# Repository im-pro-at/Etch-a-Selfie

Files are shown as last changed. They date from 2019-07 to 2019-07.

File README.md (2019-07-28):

# Etch-a-Selfie
ESP32_CAM meets Etch-A-Sketch => Etch-a-Selfie

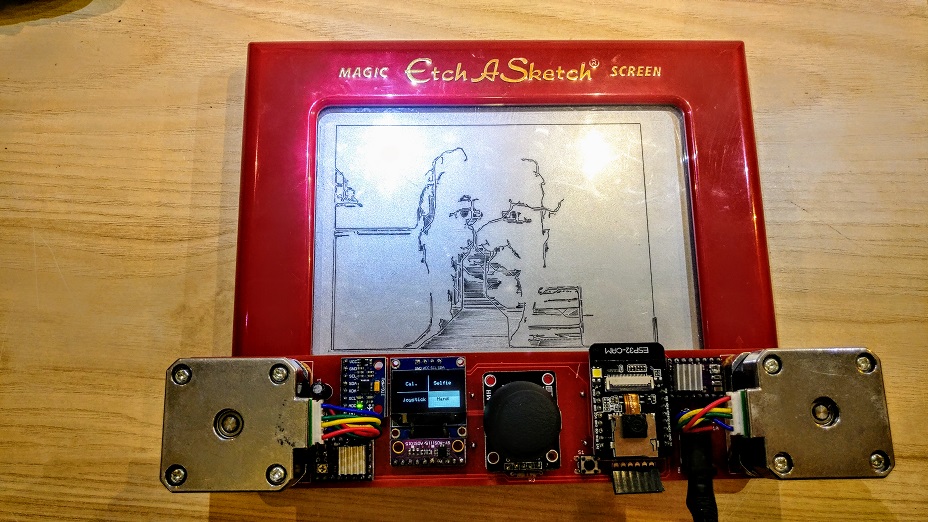
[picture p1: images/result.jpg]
result


## System Overview

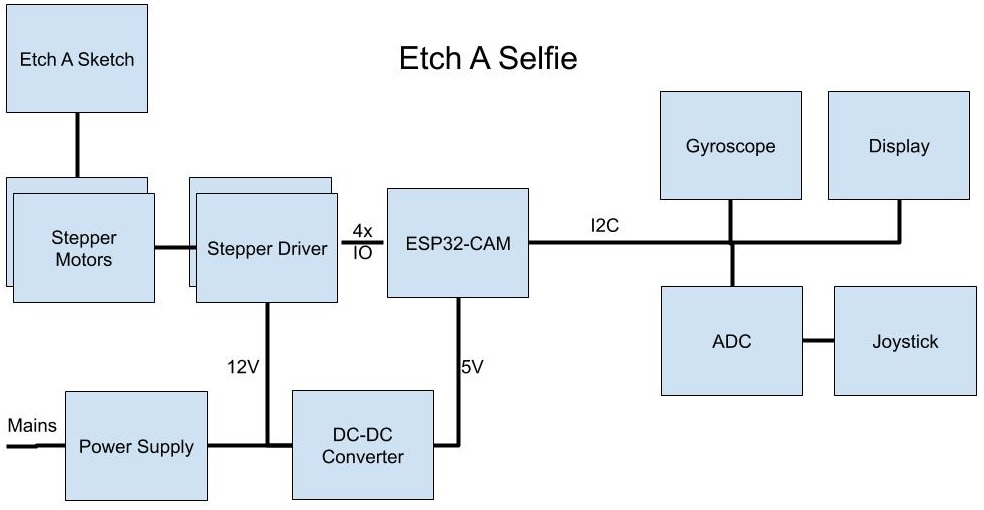
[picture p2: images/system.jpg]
system


## Software

The Software uses [GRBL](https://github.com/bdring/Grbl_Esp32) to controll the stepper motors.

A test implementation in JavaScript of the algorithms used is available [here](https://etch-a-selfie.im-pro.at/).

[Used Libraries](Sketch/ReadMe.md)

## BOM

[here](PCB/BOM.md)

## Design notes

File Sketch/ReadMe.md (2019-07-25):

# Versions 

| Name | Version |
| --- | --- |
| Arduino IDE | 1.8.9 |
| ESP32 core | 1.0.2 |
| adafruit/Adafruit-GFX-Library | 1.5.6 |
| adafruit/Adafruit_SSD1306 | 1.3.0 |
| tockn/MPU6050_tockn | 1.5.2 |
| adafruit/Adafruit_ADS1X15 | 1.0.1 |

Later Version may work but are not tested ...

# Settings

| Name | Setting |
| --- | --- |
| Board | ESP32 Wrover Module |
| Upload Speed | 921600 |
| Flash Frequency | 80MHz |
| Flash Mode | QIO |
| Partion Scheme | Huge APP (3Mb No OTA) |
| Core Debug Level | None |

# Flashing

Look [here](https://github.com/raphaelbs/esp32-cam-ai-thinker#flashing)

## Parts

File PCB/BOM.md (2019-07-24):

# Bill of materials

| # |  Price | Description |
| ---- | -----: | --- |
| 1 | 36,99€ | [Etch-A-Sketch Classic](https://www.amazon.de/Spin-Master-20083952-Etch-A-Sketch-Classic/dp/B01N1ZVYDM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) |
| 1 |  6.76€ | [PCB form JLCPCB](https://jlcpcb.com) |
| 1 |  6,21€ | [Geekcreit® ESP32-CAM WiFi + bluetooth Camera Module](https://www.banggood.com/Geekcreit-ESP32-CAM-WiFi-bluetooth-Camera-Module-Development-Board-ESP32-With-Camera-Module-OV2640-p-1394679.html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) |
| 1 |  1,40€ | [2596S LM2596S 3A Adjustable Step-down DC-DC Power Supply Module](https://www.banggood.com/1pcs-2596S-LM2596S-3A-Adjustable-Step-down-DC-DC-Power-Supply-Module-p-1213135.html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) |
| 1 |  4,43€ | [Geekcreit® 1.3 Inch 4Pin White OLED LCD Display 12864 IIC](https://www.banggood.com/1_3-Inch-4Pin-White-OLED-LCD-Display-12864-IIC-I2C-Interface-Module-For-Arduino-p-1067874.html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) |
| 1 |  1,32€ | [6DOF MPU-6050 3 Axis Gyro With Accelerometer Sensor](https://www.banggood.com/6DOF-MPU-6050-3-Axis-Gyro-With-Accelerometer-Sensor-Module-For-Arduino-p-80862.html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) |
| 1 |  1,34€ | [PS2 Game Joystick Module For Arduino](https://www.banggood.com/PS2-Game-Joystick-Module-For-Arduino-p-76465.html?rmmds=search&cur_warehouse=CN) |
| 1 |  3,53€ | [I2C ADS1115 16 Bit ADC 4 Channel Module](https://www.banggood.com/I2C-ADS1115-16-Bit-ADC-4-Channel-Module-With-Programmable-Gain-Amplifier-For-Arduino-RPi-p-1110588.html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) |
| 1 |  1,50€ | [DC Jack 5.5x2.1mm](https://www.banggood.com/10pcs-5_5-x-2_1mm-DC-Power-Supply-Female-Jack-Socket-p-1062018.html?cur_warehouse=CN) |
| 2 |  1,66€ | [5mm x 6mm Aluminum Flexible Shaft Coupling OD19mm x L25mm](https://www.banggood.com/5mm-x-6mm-Aluminum-Flexible-Shaft-Coupling-OD19mm-x-L25mm-CNC-Stepper-Motor-Coupler-Connector-p-993559.html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) |
| 2 |  2,12€ | [Geekcreit® 3D Printer Stepstick DRV8825 Stepper Driver Reprap 4 Layer PCB](https://www.banggood.com/Geekcreit-3D-Printer-Stepstick-DRV8825-Stepper-Motor-Driver-Reprap-4-Layer-PCB-p-920162.html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) |
| 2 |  6,27€ | [HANPOSE 17HS2408 28mm Nema 17 Stepper Motor 42 Motor 42BYGH 0.6A 12N.cm](https://www.banggood.com/HANPOSE-28mm-Nema-17-Stepper-Motor-42-Motor-17HS2408-42BYGH-0_6A-12N_cm-4-lead-For-CNC-Laser-3D-Printer-Motor-p-1415423.html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) |
| 1 |  3,94€ | [AC 100-240V Converter Adapter 12V 2A 24W Power Supply](https://www.banggood.com/AC-100-240V-Converter-Adapter-12V-2A-24W-Power-Supply-For-LED-Strip-p-1006925.html?ID=43100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) |
| 1 |  1,28€ | [2.54mm Single Row Male Pin Header](https://www.banggood.com/10-Pcs-40-Pin-2_54mm-Single-Row-Male-Pin-Header-Strip-For-Arduino-p-918427.html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) |
| 3 | - | 4k7 Ohm Resistor 1/4W |
| 4 | - | M3 screw 8mm length |
| 2 |  1,60€ | [Cork Gasket (Optional)](https://www.banggood.com/5PCS-4242mm-Cork-Gasket-Nema-17-Stepper-Motor-Damper-For-42-Motor-Absorber-3D-Printer-Part-p-1446977.html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) |
| 2 | - | 100µF 35V Capacitor E2,5-6 (Optional) |
| | | |
| | ~89€ | TOTAL |

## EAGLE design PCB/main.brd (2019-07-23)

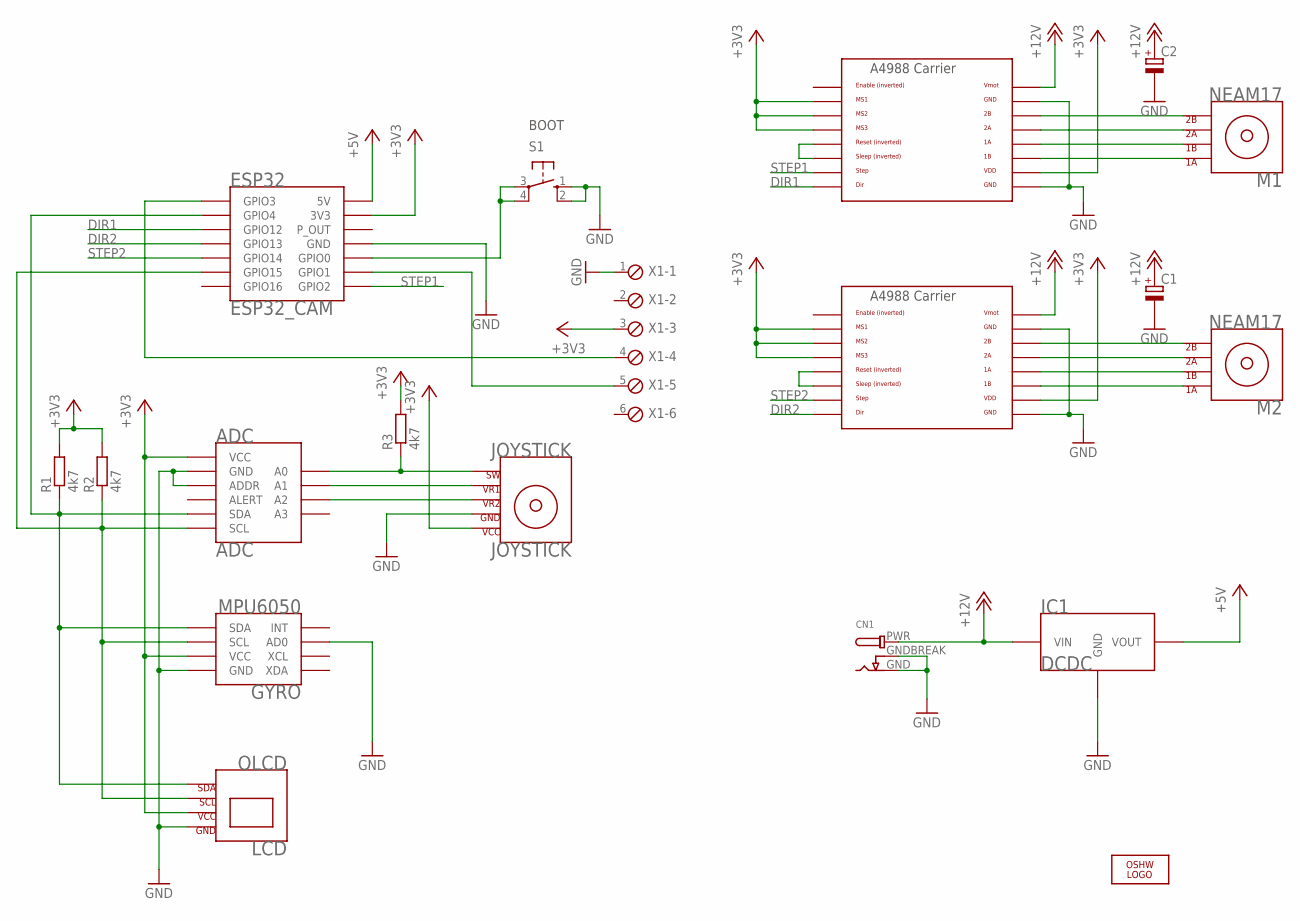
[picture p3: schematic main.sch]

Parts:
ADC: ADC
C1, C2: CPOL-EUE2.5-6; E2,5-6
CN1: DCBARRELPTH; DCJACK_2MM_PTH
ESP32: ESP32_CAM
GYRO: MPU6050
IC1: DCDC
IC2, IC3: A4988BREAKOUT
JOYSTICK: JOYSTICK
LCD: OLCD
LOGO1: OHW-LOGO_OSHW_LOGO_FILLX0350-NT; OHW-LOGO_OSHW_FILLX350_NOTEXT
M1, M2: NEAM17; NEMA17
R1, R2, R3: 4k7; 0207/10
S1: 10-XX; B3F-10XX
X1: MPT6; 6POL254

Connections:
+3V3: ADC.VCC, ESP32.3V3, GYRO.VCC, IC2.MS1, IC2.MS2, IC2.MS3, IC2.VDD, IC3.MS1, IC3.MS2, IC3.MS3, IC3.VDD, JOYSTICK.VCC, LCD.VCC, R1.2, R2.2, R3.2, X1.3
+5V: ESP32.5V, IC1.VOUT
+12V: C1.+, C2.+, CN1.PWR, IC1.VIN, IC2.VMOT, IC3.VMOT
DIR1: ESP32.GPIO12, IC2.DIR
DIR2: ESP32.GPIO13, IC3.DIR
GND: ADC.ADDR, ADC.GND, C1.-, C2.-, CN1.GND, CN1.GNDBREAK, ESP32.GND1 (GND), ESP32.GND2 (GND), ESP32.GND3 (GND), GYRO.AD0, GYRO.GND, IC1.GND1 (GND), IC1.GND2 (GND), IC2.GND, IC2.GND@0 (GND), IC3.GND, IC3.GND@0 (GND), JOYSTICK.GND, LCD.GND, S1.1 (S), S1.2 (S1), X1.1
unnamed: IC2.1B, M1.1A
unnamed: IC2.RST, IC2.SLP (SLEEP)
unnamed: IC2.2B, M1.2B
unnamed: IC2.2A, M1.2A
unnamed: IC2.1A, M1.1B
unnamed: IC3.RST, IC3.SLP (SLEEP)
unnamed: IC3.2B, M2.2B
unnamed: IC3.2A, M2.2A
unnamed: IC3.1A, M2.1B
unnamed: IC3.1B, M2.1A
unnamed: ESP32.GPIO1, X1.5
unnamed: ESP32.GPIO3, X1.4
unnamed: ESP32.GPIO0, S1.3, S1.4 (P1)
unnamed: ADC.A0, JOYSTICK.SW, R3.1
unnamed: ADC.A1, JOYSTICK.VR1
unnamed: ADC.A2, JOYSTICK.VR2
unnamed: ADC.SCL, ESP32.GPIO15, GYRO.SCL, LCD.SCL, R2.1
unnamed: ADC.SDA, ESP32.GPIO4, GYRO.SDA, LCD.SDA, R1.1
STEP1: ESP32.GPIO2, IC2.STEP
STEP2: ESP32.GPIO14, IC3.STEP

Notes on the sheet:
BOOT

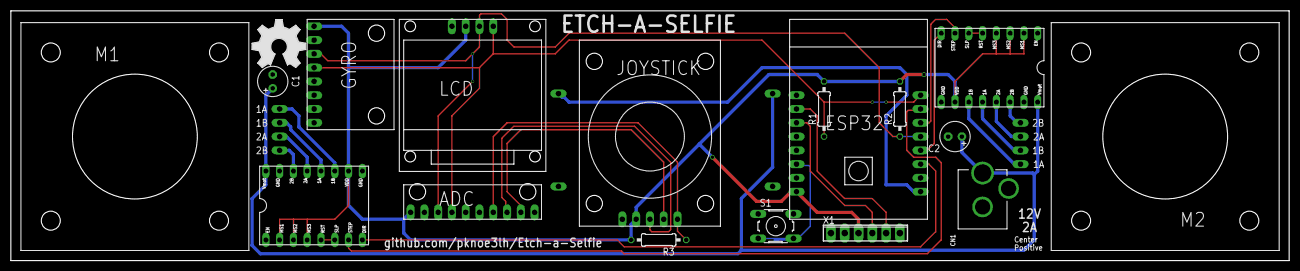
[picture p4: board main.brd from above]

Board: 2 copper layers, 235.6 x 46.0 mm, 19 parts (1 on the bottom side), 26 nets.

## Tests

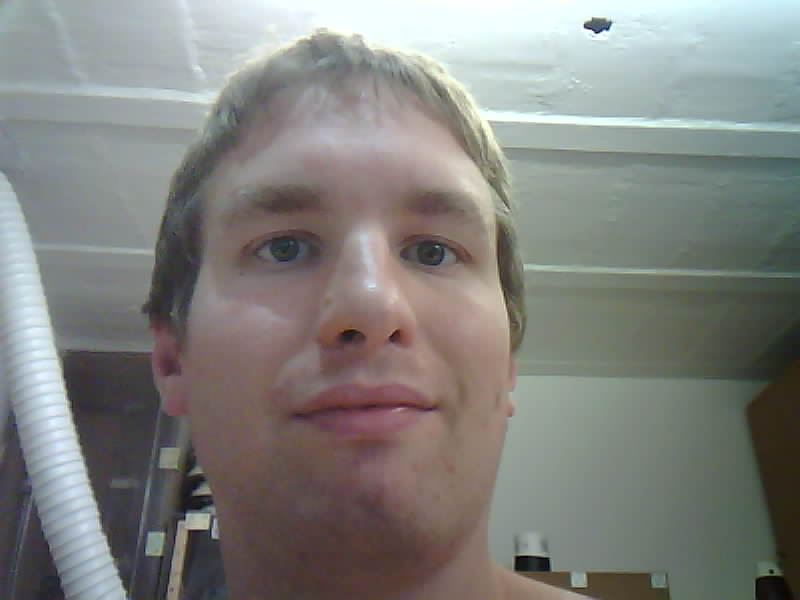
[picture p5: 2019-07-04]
AlgorithmTest/test.jpg

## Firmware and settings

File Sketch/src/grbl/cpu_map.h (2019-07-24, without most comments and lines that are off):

#ifdef CPU_MAP_ESP32
		#define CPU_MAP_NAME "CPU_MAP_ESP32"
		#define X_STEP_PIN      	GPIO_NUM_12
		#define X_DIRECTION_PIN  	GPIO_NUM_26
		#define X_RMT_CHANNEL		0
		#define Y_STEP_PIN      	GPIO_NUM_14
		#define Y_DIRECTION_PIN   	GPIO_NUM_25
		#define Y_RMT_CHANNEL		1
		#define Z_STEP_PIN      	GPIO_NUM_27
		#define Z_DIRECTION_PIN   	GPIO_NUM_33
		#define Z_RMT_CHANNEL		2
		#define STEPPERS_DISABLE_PIN GPIO_NUM_13
		#define COOLANT_FLOOD_PIN 	GPIO_NUM_16
		#define SPINDLE_PWM_PIN    GPIO_NUM_17
		#define SPINDLE_PWM_CHANNEL 0
		#define SPINDLE_PWM_BASE_FREQ 5000 // Hz
		#define SPINDLE_PWM_BIT_PRECISION 8   // be sure to match this with SPINDLE_PWM_MAX_VALUE
		#define SPINDLE_PWM_OFF_VALUE     0
		#define SPINDLE_PWM_MAX_VALUE     255 // (2^SPINDLE_PWM_BIT_PRECISION)
				#define SPINDLE_PWM_MIN_VALUE   1   // Must be greater than zero.
		#define SPINDLE_ENABLE_PIN	GPIO_NUM_22
		#define SPINDLE_PWM_RANGE         (SPINDLE_PWM_MAX_VALUE-SPINDLE_PWM_MIN_VALUE)
		#define X_LIMIT_PIN      	GPIO_NUM_2
		#define Y_LIMIT_PIN      	GPIO_NUM_4
		#define Z_LIMIT_PIN     	GPIO_NUM_15
		#define LIMIT_MASK      	B111
		#define PROBE_PIN       	GPIO_NUM_32
		#define CONTROL_SAFETY_DOOR_PIN   GPIO_NUM_35  // needs external pullup
		#define CONTROL_RESET_PIN         GPIO_NUM_34  // needs external pullup
		#define CONTROL_FEED_HOLD_PIN     GPIO_NUM_36  // needs external pullup
		#define CONTROL_CYCLE_START_PIN   GPIO_NUM_39  // needs external pullup
#endif
#ifdef CPU_MAP_ESP32_ETCH_A_SELFIE
		#define CPU_MAP_NAME "CPU_MAP_ESP32_ETCH_A_SELFIE"
		#define X_STEP_PIN      	GPIO_NUM_2
		#define X_DIRECTION_PIN  	GPIO_NUM_12
		#define Y_STEP_PIN      	GPIO_NUM_14
		#define Y_DIRECTION_PIN   GPIO_NUM_13
		#define SPINDLE_PWM_CHANNEL 0
		#define SPINDLE_PWM_BASE_FREQ 5000 // Hz
		#define SPINDLE_PWM_BIT_PRECISION 8   // be sure to match this with SPINDLE_PWM_MAX_VALUE
		#define SPINDLE_PWM_OFF_VALUE     0
		#define SPINDLE_PWM_MAX_VALUE     255 // (2^SPINDLE_PWM_BIT_PRECISION)
		#ifndef SPINDLE_PWM_MIN_VALUE
				#define SPINDLE_PWM_MIN_VALUE   1   // Must be greater than zero.
		#endif
		#define SPINDLE_PWM_RANGE         (SPINDLE_PWM_MAX_VALUE-SPINDLE_PWM_MIN_VALUE)
		#define LIMIT_MASK      	B111
		#define PROBE_PIN       	GPIO_NUM_32
		#ifdef DEFAULTS_GENERIC
			#undef DEFAULTS_GENERIC  // undefine generic then define each default below
		#endif
		#define DEFAULT_STEP_PULSE_MICROSECONDS 3
		#define DEFAULT_STEPPER_IDLE_LOCK_TIME 250 // stay on
		#define DEFAULT_STEPPING_INVERT_MASK 0 // uint8_t
		#define DEFAULT_DIRECTION_INVERT_MASK 1 // Invert x
		#define DEFAULT_INVERT_ST_ENABLE 0 // boolean
		#define DEFAULT_INVERT_LIMIT_PINS 1 // boolean
		#define DEFAULT_INVERT_PROBE_PIN 0 // boolean
		#define DEFAULT_STATUS_REPORT_MASK 1
		#define DEFAULT_JUNCTION_DEVIATION 0.01 // mm
		#define DEFAULT_ARC_TOLERANCE 0.002 // mm
		#define DEFAULT_REPORT_INCHES 0 // false
		#define DEFAULT_SOFT_LIMIT_ENABLE 0 // false
		#define DEFAULT_HARD_LIMIT_ENABLE 0  // false
		#define DEFAULT_HOMING_ENABLE 0
		#define DEFAULT_HOMING_DIR_MASK 0 // move positive dir Z, negative X,Y
		#define DEFAULT_HOMING_FEED_RATE 200.0 // mm/min
		#define DEFAULT_HOMING_SEEK_RATE 1000.0 // mm/min
		#define DEFAULT_HOMING_DEBOUNCE_DELAY 250 // msec (0-65k)
		#define DEFAULT_HOMING_PULLOFF 3.0 // mm
		#define DEFAULT_SPINDLE_RPM_MAX 1000.0 // rpm
		#define DEFAULT_SPINDLE_RPM_MIN 0.0 // rpm
		#define DEFAULT_LASER_MODE 0 // false
		#define DEFAULT_X_STEPS_PER_MM 44.44
		#define DEFAULT_Y_STEPS_PER_MM 44.44
		#define DEFAULT_Z_STEPS_PER_MM 100.0
		#define DEFAULT_X_MAX_RATE 30000.0 // mm/min
		#define DEFAULT_Y_MAX_RATE 30000.0 // mm/min
		#define DEFAULT_Z_MAX_RATE 5000.0 // mm/min
		#define DEFAULT_X_ACCELERATION (5000.0*60*60)
		#define DEFAULT_Y_ACCELERATION (5000.0*60*60)
		#define DEFAULT_Z_ACCELERATION (50.0*60*60)
		#define DEFAULT_X_MAX_TRAVEL 300.0 // mm NOTE: Must be a positive value.
		#define DEFAULT_Y_MAX_TRAVEL 300.0 // mm NOTE: Must be a positive value.
		#define DEFAULT_Z_MAX_TRAVEL 100.0 // This is percent in servo mode...used for calibration
#endif
#ifdef CPU_MAP_ESP32_ESC_SPINDLE
		#define CPU_MAP_NAME "CPU_MAP_ESP32_ESC_SPINDLE"
		#define X_STEP_PIN      	GPIO_NUM_12
		#define X_DIRECTION_PIN  	GPIO_NUM_26
		#define X_RMT_CHANNEL		0
		#define Y_STEP_PIN      	GPIO_NUM_14
		#define Y_DIRECTION_PIN   	GPIO_NUM_25
		#define Y_RMT_CHANNEL		1
		#define Z_STEP_PIN      	GPIO_NUM_27
		#define Z_DIRECTION_PIN   	GPIO_NUM_33
		#define Z_RMT_CHANNEL		2
		#define STEPPERS_DISABLE_PIN GPIO_NUM_13
		#define COOLANT_FLOOD_PIN 	GPIO_NUM_16
		#define SPINDLE_PWM_PIN    GPIO_NUM_17
		#define SPINDLE_PWM_CHANNEL 0
		#define SPINDLE_PWM_BASE_FREQ 50 // Hz for ESC
		#define SPINDLE_PWM_BIT_PRECISION 16   // 16 bit required for ESC
		#define SPINDLE_PULSE_RES_COUNT 65535
		#define ESC_MIN_PULSE_SEC 0.001 // min pulse in seconds (OK to tune this one)
		#define ESC_MAX_PULSE_SEC 0.002 // max pulse in seconds (OK to tune this one)
		#define ESC_TIME_PER_BIT  ((1.0 / (float)SPINDLE_PWM_BASE_FREQ) / ((float)SPINDLE_PULSE_RES_COUNT) ) // seconds
		#define SPINDLE_PWM_OFF_VALUE    (uint16_t)(ESC_MIN_PULSE_SEC / ESC_TIME_PER_BIT) // in timer counts
		#define SPINDLE_PWM_MAX_VALUE    (uint16_t)(ESC_MAX_PULSE_SEC / ESC_TIME_PER_BIT) // in timer counts
		#ifndef SPINDLE_PWM_MIN_VALUE
				#define SPINDLE_PWM_MIN_VALUE   SPINDLE_PWM_OFF_VALUE   // Must be greater than zero.
		#endif
		#define SPINDLE_PWM_RANGE         (SPINDLE_PWM_MAX_VALUE-SPINDLE_PWM_MIN_VALUE)
		#define SPINDLE_ENABLE_PIN	GPIO_NUM_22
		#define X_LIMIT_PIN      	GPIO_NUM_2
		#define Y_LIMIT_PIN      	GPIO_NUM_4
		#define Z_LIMIT_PIN     	GPIO_NUM_15
		#define LIMIT_MASK      	B111
		#define PROBE_PIN       	GPIO_NUM_32
		#define CONTROL_SAFETY_DOOR_PIN   GPIO_NUM_35  // needs external pullup
		#define CONTROL_RESET_PIN         GPIO_NUM_34  // needs external pullup
		#define CONTROL_FEED_HOLD_PIN     GPIO_NUM_36  // needs external pullup
		#define CONTROL_CYCLE_START_PIN   GPIO_NUM_39  // needs external pullup
#endif
#ifdef CPU_MAP_PEN_LASER  // The Buildlog.net pen laser controller V1
		#define CPU_MAP_NAME "CPU_MAP_PEN_LASER"
		#define PEN_LASER_V2
		#define X_STEP_PIN      GPIO_NUM_12
		#define Y_STEP_PIN      GPIO_NUM_14
		#define X_DIRECTION_PIN   GPIO_NUM_26
		#define Y_DIRECTION_PIN   GPIO_NUM_25
		#define STEPPERS_DISABLE_PIN GPIO_NUM_13
		#ifdef PEN_LASER_V2
			#define X_LIMIT_PIN      	GPIO_NUM_15
		#endif
		#define Y_LIMIT_PIN      	GPIO_NUM_4
		#define LIMIT_MASK      	B11
		#define SPINDLE_PWM_PIN    GPIO_NUM_17 // Laser PWM
		#define SPINDLE_PWM_CHANNEL 0
		#define SPINDLE_PWM_BASE_FREQ 5000 // Hz
		#define SPINDLE_PWM_BIT_PRECISION 8   // be sure to match this with SPINDLE_PWM_MAX_VALUE
		#define SPINDLE_PWM_OFF_VALUE     0
		#define SPINDLE_PWM_MAX_VALUE     255 // (2^SPINDLE_PWM_BIT_PRECISION)
		#ifndef SPINDLE_PWM_MIN_VALUE
				#define SPINDLE_PWM_MIN_VALUE   1   // Must be greater than zero.
		#endif
		#define SPINDLE_PWM_RANGE         (SPINDLE_PWM_MAX_VALUE-SPINDLE_PWM_MIN_VALUE)
		#define SERVO_PEN_PIN 					GPIO_NUM_27
		#ifdef DEFAULTS_GENERIC
			#undef DEFAULTS_GENERIC  // undefine generic then define each default below
		#endif
		#define DEFAULT_STEP_PULSE_MICROSECONDS 3
		#define DEFAULT_STEPPER_IDLE_LOCK_TIME 250 // stay on
		#define DEFAULT_STEPPING_INVERT_MASK 0 // uint8_t
		#define DEFAULT_DIRECTION_INVERT_MASK 0 // uint8_t
		#define DEFAULT_INVERT_ST_ENABLE 0 // boolean
		#define DEFAULT_INVERT_LIMIT_PINS 1 // boolean
		#define DEFAULT_INVERT_PROBE_PIN 0 // boolean
		#define DEFAULT_STATUS_REPORT_MASK 1
		#define DEFAULT_JUNCTION_DEVIATION 0.01 // mm
		#define DEFAULT_ARC_TOLERANCE 0.002 // mm
		#define DEFAULT_REPORT_INCHES 0 // false
		#define DEFAULT_SOFT_LIMIT_ENABLE 0 // false
		#define DEFAULT_HARD_LIMIT_ENABLE 0  // false
		#define DEFAULT_HOMING_ENABLE 0
		#define DEFAULT_HOMING_DIR_MASK 0 // move positive dir Z, negative X,Y
		#define DEFAULT_HOMING_FEED_RATE 200.0 // mm/min
		#define DEFAULT_HOMING_SEEK_RATE 1000.0 // mm/min
		#define DEFAULT_HOMING_DEBOUNCE_DELAY 250 // msec (0-65k)
		#define DEFAULT_HOMING_PULLOFF 3.0 // mm
		#define DEFAULT_SPINDLE_RPM_MAX 1000.0 // rpm
		#define DEFAULT_SPINDLE_RPM_MIN 0.0 // rpm
		#define DEFAULT_LASER_MODE 0 // false
		#define DEFAULT_X_STEPS_PER_MM 80
		#define DEFAULT_Y_STEPS_PER_MM 80
		#define DEFAULT_Z_STEPS_PER_MM 100.0 // This is percent in servo mode...used for calibration
		#define DEFAULT_X_MAX_RATE 5000.0 // mm/min
		#define DEFAULT_Y_MAX_RATE 5000.0 // mm/min
		#define DEFAULT_Z_MAX_RATE 5000.0 // mm/min
		#define DEFAULT_X_ACCELERATION (50.0*60*60) // 10*60*60 mm/min^2 = 10 mm/sec^2
		#define DEFAULT_Y_ACCELERATION (50.0*60*60) // 10*60*60 mm/min^2 = 10 mm/sec^2
		#define DEFAULT_Z_ACCELERATION (50.0*60*60)
		#define DEFAULT_X_MAX_TRAVEL 300.0 // mm NOTE: Must be a positive value.
		#define DEFAULT_Y_MAX_TRAVEL 300.0 // mm NOTE: Must be a positive value.
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

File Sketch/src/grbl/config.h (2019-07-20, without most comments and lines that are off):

#define config_h
#include "grbl.h" // For Arduino IDE compatibility.
#define ESP_DEBUG
#define DEFAULTS_GENERIC
#define CPU_MAP_ESP32_ETCH_A_SELFIE // these are defined in cpu_map.h
#define VERBOSE_HELP // adds addition help info, but could confuse some senders
#define BAUD_RATE 115200
#define NAMESPACE "GRBL"
#define ESP_RADIO_MODE "RADIO_MODE"
#define ESP_RADIO_OFF 0
#define ESP_WIFI_STA 1
#define ESP_WIFI_AP  2
#define ESP_BT       3
    #undef ENABLE_NOTIFICATIONS
    #define DEFAULT_RADIO_MODE ESP_RADIO_OFF
#define CMD_RESET 0x18 // ctrl-x.
#define CMD_STATUS_REPORT '?'
#define CMD_CYCLE_START '~'
#define CMD_FEED_HOLD '!'
#define CMD_SAFETY_DOOR 0x84
#define CMD_JOG_CANCEL  0x85
#define CMD_DEBUG_REPORT 0x86 // Only when DEBUG enabled, sends debug report in '{}' braces.
#define CMD_FEED_OVR_RESET 0x90         // Restores feed override value to 100%.
#define CMD_FEED_OVR_COARSE_PLUS 0x91
#define CMD_FEED_OVR_COARSE_MINUS 0x92
#define CMD_FEED_OVR_FINE_PLUS  0x93
#define CMD_FEED_OVR_FINE_MINUS  0x94
#define CMD_RAPID_OVR_RESET 0x95        // Restores rapid override value to 100%.
#define CMD_RAPID_OVR_MEDIUM 0x96
#define CMD_RAPID_OVR_LOW 0x97
#define CMD_SPINDLE_OVR_RESET 0x99      // Restores spindle override value to 100%.
#define CMD_SPINDLE_OVR_COARSE_PLUS 0x9A
#define CMD_SPINDLE_OVR_COARSE_MINUS 0x9B
#define CMD_SPINDLE_OVR_FINE_PLUS 0x9C
#define CMD_SPINDLE_OVR_FINE_MINUS 0x9D
#define CMD_SPINDLE_OVR_STOP 0x9E
#define CMD_COOLANT_FLOOD_OVR_TOGGLE 0xA0
#define CMD_COOLANT_MIST_OVR_TOGGLE 0xA1
#define HOMING_INIT_LOCK // Comment to disable
#define HOMING_CYCLE_0 (1<<Z_AXIS)                // REQUIRED: First move Z to clear workspace.
#define HOMING_CYCLE_1 (1<<X_AXIS)
#define HOMING_CYCLE_2 (1<<Y_AXIS)
#define N_HOMING_LOCATE_CYCLE 1 // Integer (1-128)
#define HOMING_SINGLE_AXIS_COMMANDS // Default disabled. Uncomment to enable.
#define N_STARTUP_LINE 2 // Integer (1-2)
#define N_DECIMAL_COORDVALUE_INCH 4 // Coordinate or position value in inches
#define N_DECIMAL_COORDVALUE_MM   3 // Coordinate or position value in mm
#define N_DECIMAL_RATEVALUE_INCH  1 // Rate or velocity value in in/min
#define N_DECIMAL_RATEVALUE_MM    0 // Rate or velocity value in mm/min
#define N_DECIMAL_SETTINGVALUE    3 // Decimals for floating point setting values
#define N_DECIMAL_RPMVALUE        0 // RPM value in rotations per min.
#define ENABLE_SAFETY_DOOR_INPUT_PIN // ESP32 Leave this enabled for now .. code for undefined not ready
#define SAFETY_DOOR_SPINDLE_DELAY 4.0 // Float (seconds)
#define SAFETY_DOOR_COOLANT_DELAY 1.0 // Float (seconds)
#define INVERT_CONTROL_PIN_MASK   B1111
#define IGNORE_CONTROL_PINS
#define CHECK_LIMITS_AT_INIT
#define DEFAULT_FEED_OVERRIDE           100 // 100%. Don't change this value.
#define MAX_FEED_RATE_OVERRIDE          200 // Percent of programmed feed rate (100-255). Usually 120% or 200%
#define MIN_FEED_RATE_OVERRIDE           10 // Percent of programmed feed rate (1-100). Usually 50% or 1%
#define FEED_OVERRIDE_COARSE_INCREMENT   10 // (1-99). Usually 10%.
#define FEED_OVERRIDE_FINE_INCREMENT      1 // (1-99). Usually 1%.
#define DEFAULT_RAPID_OVERRIDE  100 // 100%. Don't change this value.
#define RAPID_OVERRIDE_MEDIUM    50 // Percent of rapid (1-99). Usually 50%.
#define RAPID_OVERRIDE_LOW       25 // Percent of rapid (1-99). Usually 25%.
#define DEFAULT_SPINDLE_SPEED_OVERRIDE    100 // 100%. Don't change this value.
#define MAX_SPINDLE_SPEED_OVERRIDE        200 // Percent of programmed spindle speed (100-255). Usually 200%.
#define MIN_SPINDLE_SPEED_OVERRIDE         10 // Percent of programmed spindle speed (1-100). Usually 10%.
#define SPINDLE_OVERRIDE_COARSE_INCREMENT  10 // (1-99). Usually 10%.
#define SPINDLE_OVERRIDE_FINE_INCREMENT     1 // (1-99). Usually 1%.
#define RESTORE_OVERRIDES_AFTER_PROGRAM_END // Default enabled. Comment to disable.
#define REPORT_FIELD_BUFFER_STATE // Default enabled. Comment to disable.
#define REPORT_FIELD_PIN_STATE // Default enabled. Comment to disable.
#define REPORT_FIELD_CURRENT_FEED_SPEED // Default enabled. Comment to disable.
#define REPORT_FIELD_WORK_COORD_OFFSET // Default enabled. Comment to disable.
#define REPORT_FIELD_OVERRIDES // Default enabled. Comment to disable.
#define REPORT_FIELD_LINE_NUMBERS // Default enabled. Comment to disable.
#define REPORT_OVR_REFRESH_BUSY_COUNT 20  // (1-255)
#define REPORT_OVR_REFRESH_IDLE_COUNT 10  // (1-255) Must be less than or equal to the busy count
#define REPORT_WCO_REFRESH_BUSY_COUNT 30  // (2-255)
#define REPORT_WCO_REFRESH_IDLE_COUNT 10  // (2-255) Must be less than or equal to the busy count
#define ACCELERATION_TICKS_PER_SECOND 100
#define ADAPTIVE_MULTI_AXIS_STEP_SMOOTHING  // Default enabled. Comment to disable.
#define TOOL_LENGTH_OFFSET_AXIS Z_AXIS // Default z-axis. Valid values are X_AXIS, Y_AXIS, or Z_AXIS.
#define MINIMUM_JUNCTION_SPEED 0.0 // (mm/min)
#define MINIMUM_FEED_RATE 1.0 // (mm/min)
#define N_ARC_CORRECTION 12 // Integer (1-255)
#define ARC_ANGULAR_TRAVEL_EPSILON 5E-7 // Float (radians)
#define DWELL_TIME_STEP 50 // Integer (1-255) (milliseconds)
 #define RX_BUFFER_SIZE 1 // (1-254) Uncomment to override defaults in serial.h
#define DEBOUNCE_PERIOD 32 // in milliseconds default 32 microseconds
#define ENABLE_RESTORE_EEPROM_WIPE_ALL         // '$RST=*' Default enabled. Comment to disable.
#define ENABLE_RESTORE_EEPROM_DEFAULT_SETTINGS // '$RST=$' Default enabled. Comment to disable.
#define ENABLE_RESTORE_EEPROM_CLEAR_PARAMETERS // '$RST=#' Default enabled. Comment to disable.
#define ENABLE_BUILD_INFO_WRITE_COMMAND // '$I=' Default enabled. Comment to disable.
#define FORCE_BUFFER_SYNC_DURING_EEPROM_WRITE // Default enabled. Comment to disable.
#define FORCE_BUFFER_SYNC_DURING_WCO_CHANGE // Default enabled. Comment to disable.
#define PARKING_AXIS Z_AXIS // Define which axis that performs the parking motion
#define PARKING_TARGET -5.0 // Parking axis target. In mm, as machine coordinate [-max_travel,0].
#define PARKING_RATE 500.0 // Parking fast rate after pull-out in mm/min.
#define PARKING_PULLOUT_RATE 100.0 // Pull-out/plunge slow feed rate in mm/min.
#define PARKING_PULLOUT_INCREMENT 5.0 // Spindle pull-out and plunge distance in mm. Incremental distance.
#define DISABLE_LASER_DURING_HOLD // Default enabled. Comment to disable.
#define N_PIECES 4  // Integer (1-4). Number of piecewise lines used in script solution.
#define RPM_MAX  11686.4  // Max RPM of model. $30 > RPM_MAX will be limited to RPM_MAX.
#define RPM_MIN  202.5    // Min RPM of model. $31 < RPM_MIN will be limited to RPM_MIN.
#define RPM_POINT12  6145.4  // Used N_PIECES >=2. Junction point between lines 1 and 2.
#define RPM_POINT23  9627.8  // Used N_PIECES >=3. Junction point between lines 2 and 3.
#define RPM_POINT34  10813.9 // Used N_PIECES = 4. Junction point between lines 3 and 4.
#define RPM_LINE_A1  3.197101e-03  // Used N_PIECES >=1. A and B constants of line 1.
#define RPM_LINE_B1  -3.526076e-1
#define RPM_LINE_A2  1.722950e-2   // Used N_PIECES >=2. A and B constants of line 2.
#define RPM_LINE_B2  8.588176e+01
#define RPM_LINE_A3  5.901518e-02  // Used N_PIECES >=3. A and B constants of line 3.
#define RPM_LINE_B3  4.881851e+02
#define RPM_LINE_A4  1.203413e-01  // Used N_PIECES = 4. A and B constants of line 4.
#define RPM_LINE_B4  1.151360e+03

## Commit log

2019-06-30 Add PCB
    [main.brd, main.sch]
2019-06-30 Added GRBL source to be used to control the stepper motors
2019-07-01 moved grbl to the src folder
    [config.h, cpu_map.h, defaults.h]
2019-07-01 Use grbl as a library ...
2019-07-04 PIN 16 is used by PSRAM ...
    [main.brd, main.sch]
2019-07-04 We have an algorihm! Now test it on the ESP32 ...
2019-07-08 change debug port voltage to 3v3
    [main.brd, main.sch]
2019-07-13 fixed some problems with GRBL .. not perfect but should work now
    [config.h]
2019-07-15 again tried to fix grbl step pulse jitter
2019-07-17 More grbl tweaking ....
2019-07-17 Added missing ground connection on the jostick
    [main.brd, main.sch]
2019-07-19 more grbl fun ...
2019-07-20 More GUI stuff
    [config.h, cpu_map.h]
2019-07-21 better preview, add backlash compensation (not finished)
    [cpu_map.h]
2019-07-23 lesson learned from prototype
    [main.brd, main.sch]
2019-07-23 more GUI and optimisation, backlash comp is working now
    [cpu_map.h]
2019-07-23 add job file for gerber generation
    [main.brd]
2019-07-24 more little updates
    [cpu_map.h]
2019-07-25 This is it => V1
    [main.sch]
2019-07-30 different versions => different PCBs
    [main_209.brd]

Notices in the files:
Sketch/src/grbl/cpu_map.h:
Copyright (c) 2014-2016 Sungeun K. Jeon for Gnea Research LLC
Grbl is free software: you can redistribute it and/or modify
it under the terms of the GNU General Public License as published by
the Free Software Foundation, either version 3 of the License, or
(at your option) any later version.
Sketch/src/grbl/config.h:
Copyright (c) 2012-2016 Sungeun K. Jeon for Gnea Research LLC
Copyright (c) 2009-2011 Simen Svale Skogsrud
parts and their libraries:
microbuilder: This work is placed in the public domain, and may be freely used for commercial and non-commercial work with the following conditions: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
